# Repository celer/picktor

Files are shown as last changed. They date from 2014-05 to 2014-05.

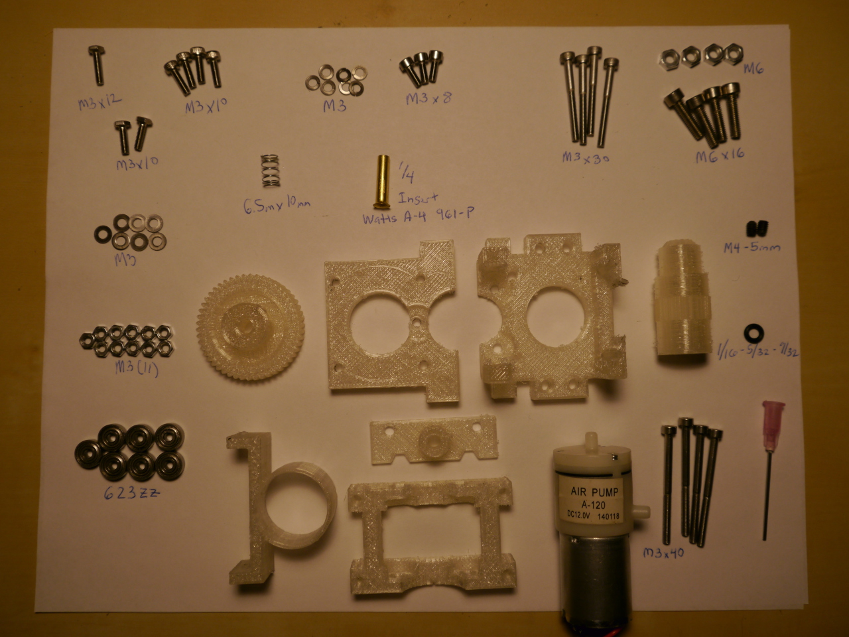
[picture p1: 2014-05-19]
images/parts.jpg

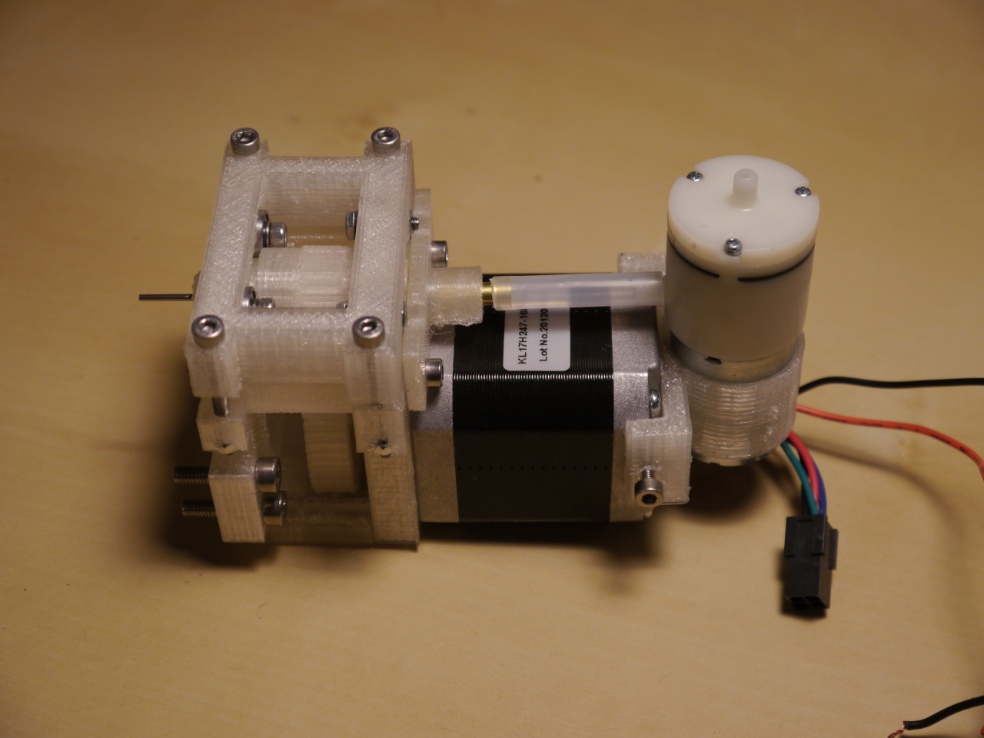
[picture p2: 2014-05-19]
images/left_side.jpg

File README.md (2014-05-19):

Introduction
============

Picktor is a 3D printable pick and place head for surface mount electronics components. 

It mounts on a 3D printer and uses a needle and vacuum pump to pick up small components and place them on a circuit board. 

To keep things simple the included software assumes you've taped/attached one or more circuit boards and bits of 
component tape to your print bed, and then told the software where your circuit boards and component tapes are. 

You can see it work here:

Video of it working (http://www.youtube.com/watch?v=OV2Zr3X-EQc)

*While I've tested this and it seems to work for me consider it a proof of concept, it may not work for you, it may break your printer, it may ruin your circuit boards...*

Modifying the 3D model
======================

Modify the model/picktor.scad, and run Make

Building the Picktor PNP Head
=============================

Here is what you'll need

![Parts] (https://raw.githubusercontent.com/celer/picktor/master/images/parts.jpg)

  * A 3D printer
  * All the parts in the model directory printed out
  * 4x M3 x 40MM Cap screws [1]
  * 7x 623ZZ Bearings [2]
  * 11x M3 nuts [3]
  * 7x M3 flat washers [3]
  * 7x M3 lock washers [3]
  * 3x M3 x 10MM hex head screws [3]
  * 4x M3 x 10MM cap head screws [1]
  * 3x M3 x 8MM cap screws [1]
  * 4x M3 x 30MM cap screws [1]
  * 2x M4 x 5MM set screws 
  * 1x 1/16 x 5/32 x 9/32 o-ring [4]
  * 6.5mm x 10mm spring [5]
  * 1/4 Brass insert from the Watts A-4 961 P plumbing kit [6]
  * 12v Vacuum Pump [7]
  * 18guage dispensing needle 
  * 1/4 ID nylon hose 
  * white lithium grease

### Where to get stuff

  - [1] http://www.ebay.com/itm/M3-0-50-X-6MM-THRU-30MM-STAINLESS-STEEL-METRIC-SOCKET-HEAD-C-S-ASSORTMENT-/291147199149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
  - [2] http://www.amazon.com/Bearing-Shielded-Miniature-Bearings-VXB/dp/B002BBF3JO/ref=sr\_1\_1?ie=UTF8&qid=1400472770&sr=8-1&keywords=623zz
  - [3] http://www.ebay.com/itm/M3-0-50-X-6MM-THRU-20MM-STAINLESS-STEEL-HEX-HEAD-CAP-SCREW-BOLT-ASSORTMENT-/291140653858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
  - [4] http://www.harborfreight.com/382-piece-o-ring-assortment-67554.html
  - [5] http://www.amazon.com/Tradespro-835798-Spring-Assortment-200-Piece/dp/B003L0LEJM/ref=sr\_1\_1?s=hi&ie=UTF8&qid=1400472954&sr=1-1&keywords=835798
  - [6] http://www.homedepot.com/p/Watts-1-4-in-Brass-Compression-Nut-with-Insert-A-4/100638289
  - [7] http://www.ebay.com/itm/DC12V-DC-micro-vacuum-pump-Pumping-air-pump-30Kpa-Air-sampling-/191113084674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
  - [8] http://www.amazon.com/XCSOURCE%C2%AE-Waterproof-Microscope-Inspection-Borescope/dp/B00JD4Y56Y/ref=sr\_1\_sc\_1?s=industrial&ie=UTF8&qid=1400475218&sr=1-1-spell&keywords=xcsouce+microscope

### Optional Items
 
  * 1 USB camera [8]

(This camera is kind of dissapointing ... see the video quality in the link above)

For mounting to the printer

  * 4x M6x16 cap head screws
  * 4x M6 nuts

Things you might have from your existing printer

  * NEMA 17 stepper motor

### Assembling the top mount

Put an M3 nut in the recessed part of the top mount. In order place a lock washer, 623ZZ bearing 
and flat washer on an M3x10 hex head bolt. Then screw the M3 bolt into the recessed nut. 

### Assemble the stepper gear

Insert the two M4 x 5MM set screws into the stepper gear. You may need an M4 tap to properly thread
the set screws into the gear. 

### Place the top mount on the stepper

Place the top mount on the stepper motor, so that the recessed nut is pressed against the stepper
motor. (It may require some pressure to put the top mount on the stepper motor. 
 
### Place the stepper gear on the stepper motor

Place the stepper gear on the stepper motor shaft, but do not tighten the set screws yet. 

### Assemble the bottom mount

Insert two M3 nuts into the recessed cut outs on the bottom of the mount. Assemble two sets of screws and bearings. 

Place a lock washer, bearing and flat washer on an M3 x 10MM cap screw and screw them into the recessed nuts on the mount.

### Put the top and bottom mount together

Place the bottom mount on the top mount and screw them togther using the 4 M3 X 40MM screws. 

### Assemble the front mount

Place 4 M3 nuts on the recessed cut outs.

Assemble 4 sets of M3 x 10mm bolts (two hex head and two cap screw) with washers and bearings. 

Utilize the 2 hex head bolts on the top part of the front mount (it has a larger diameter circle cut out of it)

Utilize the 2 cap screws on the bottom part of the front mount. 

### Prepare the tool gear

File and sand the surfaces of the tool gear that contact the bearings. 

Insert the 17 gauge need into the center of the tool gear (you may need to drill out the hole
in the tool gear). Using white lithium grease grease the o-ring and press it on top of the 17 gauge
needle. The o-ring must press on the top of the needle opening (the pink part). Apply grease to the
top of the o-ring.

Using a marker, mark the top of the tool gear on one of the lines. 

### Place the tool gear between the front mount and mounts attached to the stepper motor. 

Place the tool gear between the front mount and mounts attached to the stepper motor. 
Adjust the stepper gear so that the teeth on the stepper gear align with the teeth on the tool gear - tighten the set screws. 

Check to make sure that the tool gear spins freely, if not check for clearences against the various bolt heads, uneven surfaces
on the tool gear and lastly that all the bearings spin freely. 

### Attach the front mount to the other mounts

Place the 4 M3 nuts into the recessed cut outs on the front of the bottom mount. 

Using the 4 M3 x 30 MM screws attach the front mount to the bottom mount. 

### Assemble the air house mount

Place the spring on top of the brass insert, and then insert into the printed air hose mount. Attach the air house mount to the top of the top mount using 2 M3x8MM cap head screws. The brass insert
should press against the top of the o-ring in the tool gear. 

### Assemble the pump mount

Thread an M3 X 8mm screw into one of the holes on the side of the air pump mount. 

Insert the vacuum pump into the vacuum pump mount. Place the vacuum pump mount on top of the stepper motor, and cut an appropriate length of 1/4 nylon hose to fit between the pump and
air hose mount. 

Using it
========

 *There is no warranty, use this at your own risk*
 
### Attach the picktor head to your 3D printer

In the model/picktor.scad file there is a function mount\_ordbot which generates the appropriate
mount setup for the ordbot, create a new function which is appropriate for your printer. 

### Wire up the stepper motor to where your extruder was

If you used the same stepper motor which powered your extruder, then simply hook it back up. 

### Attach the vacuum pump to one of the power supplies (I used the power supply which was running the fan for my extruder)

You'll need some way to to turn on and off the vacuum pump. On my printer I'm using the same pins that were used to power
the cooling fan for the extruder. In my case it is PIN 4 and I use the gcode command 'M42 P4 S255' to turn on and off the vacuum pump. 

Both Marlin and Sprinter firmware don't buffer the M42 command, so you will need to modify your firmware to call st\_synchronize(); immediately after
the M42 command is recieved.

In sprinter, this functionality can be enabled by enabling the macro CHAIN\_OF\_COMMAND

https://github.com/kliment/Sprinter/blob/master/Sprinter/Sprinter.pde#L1446

In Marlin you'll need to add the line st\_synchronize()

https://github.com/ErikZalm/Marlin/blob/Marlin_v1/Marlin/Marlin_main.cpp#L1798

It should look like this after your modification:

```c
    case 42: //M42 -Change pin status via gcode
      if (code_seen('S'))
      {
        int pin_status = code_value();
        int pin_number = LED_PIN;

        st_synchronize();

      //...
```

### Level our printer bed so that it just barely touches the placer needle

The included software in /src is designed to utilize a needle which almost touches the print bed. 

### Configure the software

To run the included software you'll need Python 2.7 and to create an appropriate configuration file. 

So the software makes some assumptions, it assumes that you've taped your circuit board(s) to the print bed, along with some 
component tapes. And that you've put some basic reference information in the config.yml.

### Tape the circuit board to your printer bed

Tape one or more circuit boards to your print bed. And in the config.yml specify the location of a single component 
on the board. Once you run the software it will tell you where it expects the second reference to be on your print bed. 

### Tape the component tapes to your printer bed

Tape one or more tapes of componets to your print bed. Specify in the config software where the first component is 
on the print bed. Once you run the software it will tel you where it expects the last component to be on the print bed.

### Print! 

Do a few test runs before you assume all is good!

### Adjust any out of place components

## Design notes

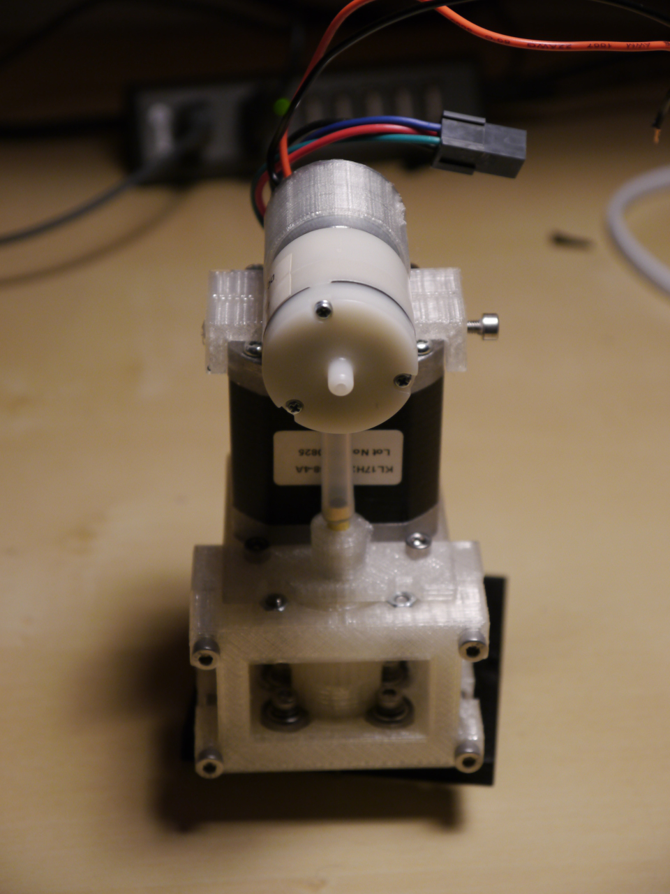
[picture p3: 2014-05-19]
images/front.jpg

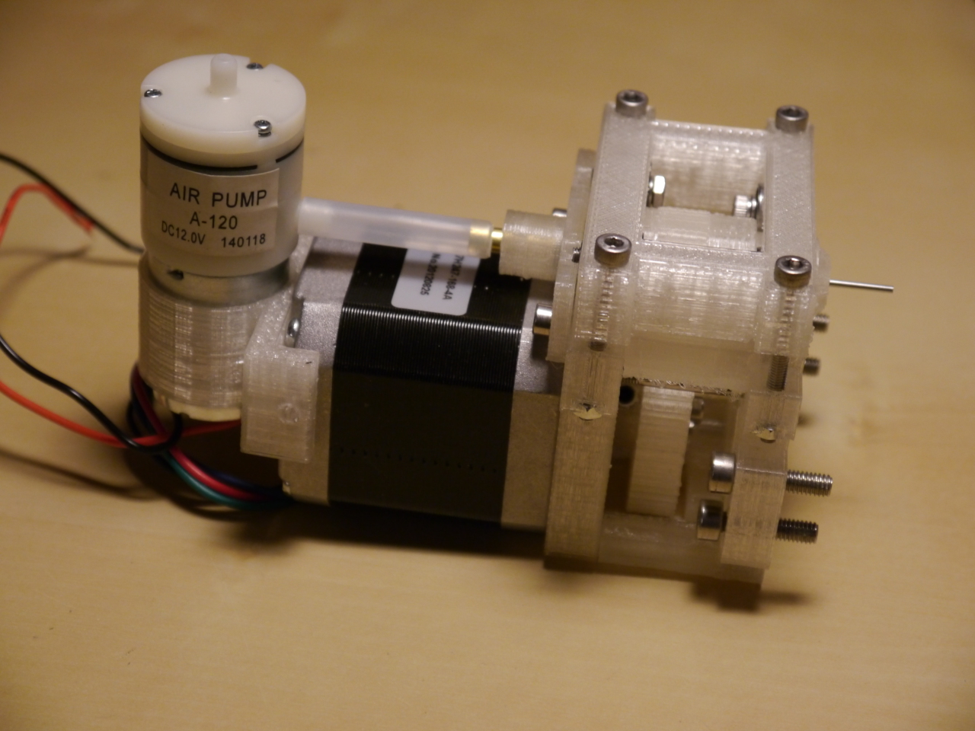
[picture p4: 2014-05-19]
images/right_side.jpg

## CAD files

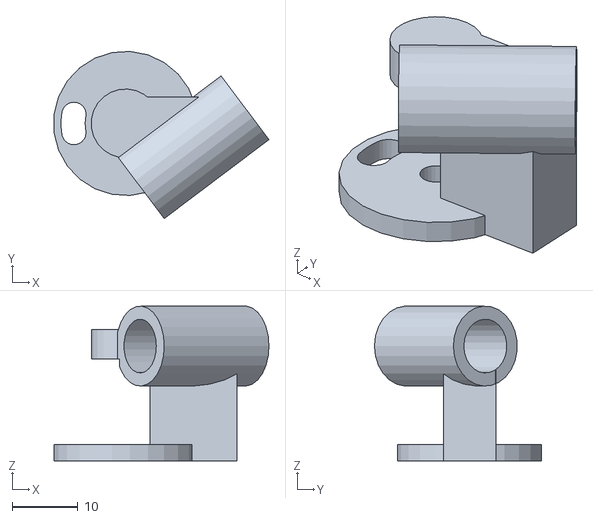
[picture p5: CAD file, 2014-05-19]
model/picktor_camera_mount.stl
32.8 x 25.5 x 23.6

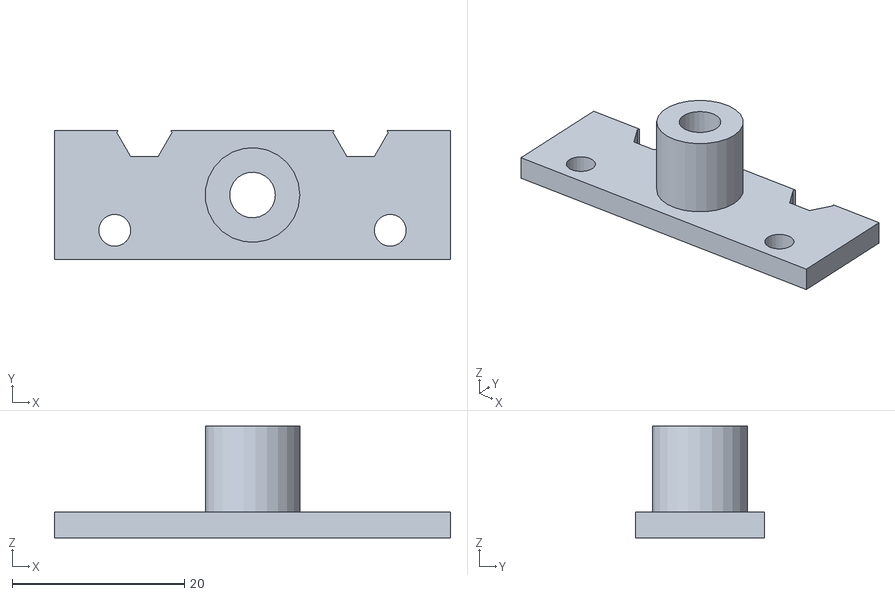
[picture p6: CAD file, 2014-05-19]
model/picktor_air_hose_mount.stl
46.0 x 15.0 x 13.0

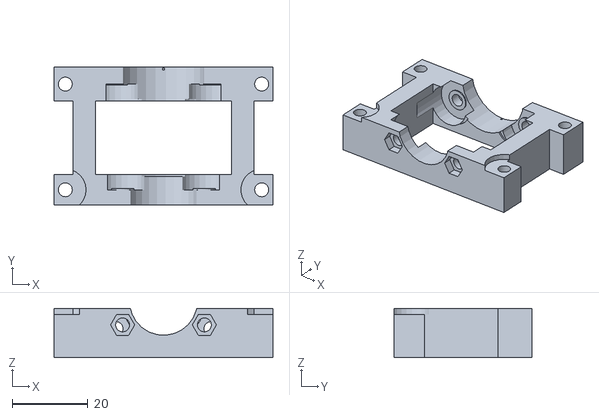
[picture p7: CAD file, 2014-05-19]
model/picktor_mount_front.stl
58.0 x 36.5 x 13.0

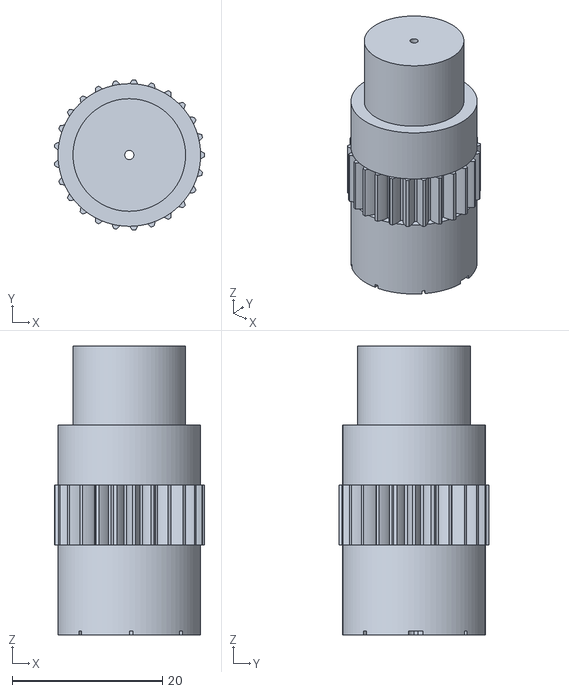
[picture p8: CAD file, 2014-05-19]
model/picktor_tool_gear.stl
20.0 x 20.0 x 38.5

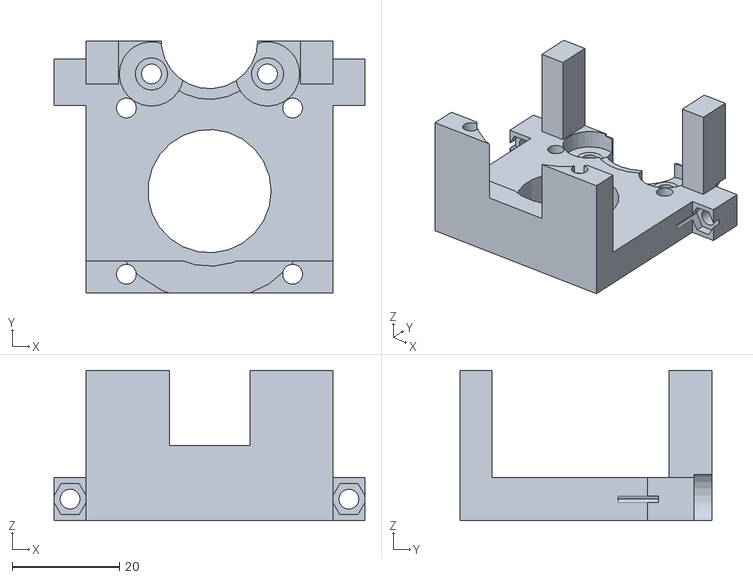
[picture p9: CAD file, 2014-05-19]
model/picktor_mount_bottom.stl
58.0 x 47.0 x 28.0

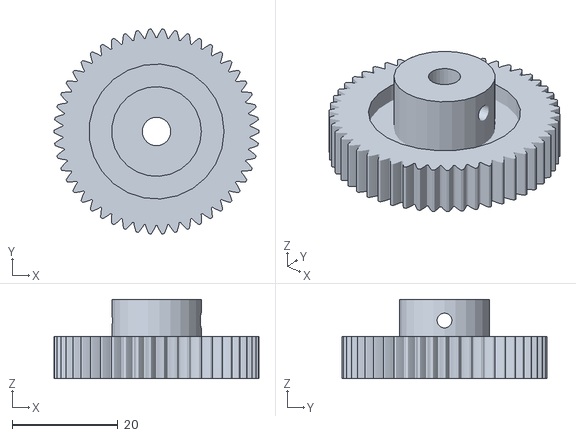
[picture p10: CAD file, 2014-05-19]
model/picktor_stepper_gear.stl
38.8 x 38.8 x 15.0

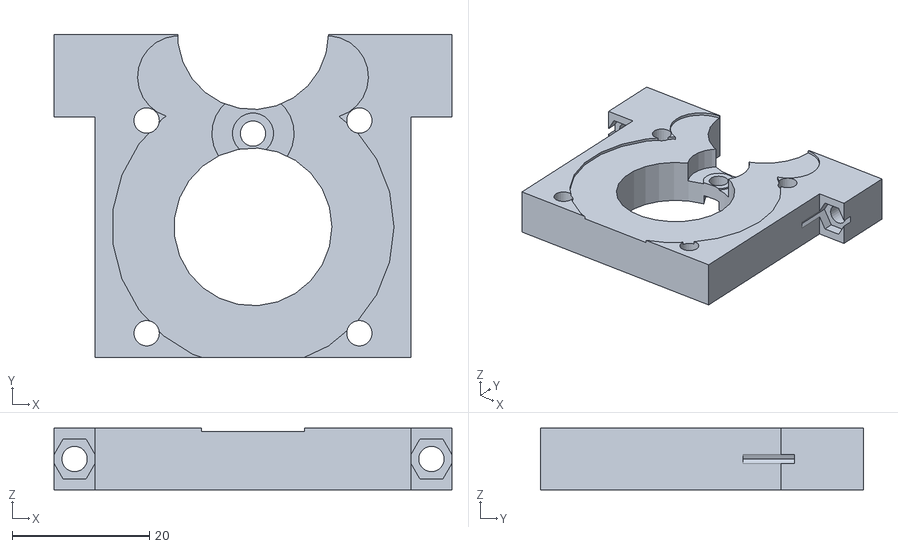
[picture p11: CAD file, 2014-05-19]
model/picktor_mount_top.stl
58.0 x 47.0 x 9.00

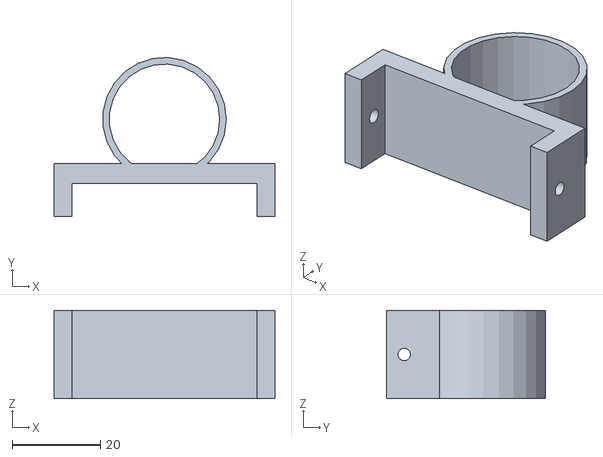
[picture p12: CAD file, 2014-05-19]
model/picktor_pump_mount.stl
50.0 x 36.0 x 20.0

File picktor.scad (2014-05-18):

//If these don't load for you, make sure you have the latest version of openscad
include <MCAD/involute_gears.scad>;
include <MCAD/stepper.scad>;
include <MCAD/nuts_and_bolts.scad>;

//Set the fineness
$fn=25;


//How far the tool gear is from the stepper gear
gear_offset=28.1;
//Top and bottom tool gear diameters
tool_top_gear_diameter=19;
tool_bottom_gear_diameter=15;


needle_diameter=1.23;


//Setup for M3 hardware
screw_size=3;
screw_hole=3.7;
screw_hole_threaded=2.8;
screw_cap=6.5;
screw_cap_height=4;

module bearing_cutout(){
	difference(){
		cylinder(r=12/2,h=4,center=true);
		translate([0,0,-4/2]) cylinder(r=6/2,h=0.6,center=true);
		translate([0,0,4/2]) cylinder(r=6/2,h=0.6,center=true);
	}
}

module bearing_screw_cutout(screw_length=15,nut_hole_depth=0){
	translate([0,0,-2]){
		translate([0,0,3.5]) cylinder(r=screw_cap/2,h=screw_cap_height);
		translate([0,0,-screw_length+4]) cylinder(r=screw_hole/2,h=screw_length);
		for(i=[0:1:nut_hole_depth]){
			rotate([0,0,30]) translate([0,0,-screw_length+4-i]) nutHole(screw_size);
		}
	}
}

module brass_stub(){
	cylinder(r=(4.4+0.90)/2,h=18.7);
	translate([0,0,18.7-6]) cylinder(r=7/2,h=6);
}

module picker_needle(n=needle_diameter){
  translate([0,0,0]) cylinder(r=7.8/2,h=2.5);
  translate([0,0,2.5]) cylinder(r1=6.8/2,r2=6.5/2,h=17);
  cylinder(r=n/2,h=50.50);
}

module tool_gear(n=needle_diameter){
	difference(){
		union(){
			gear(circular_pitch=135,number_of_teeth=25,hub_thickness=0,bore_diameter=5.40,rim_thicknes=15);
			translate([0,0,14]) cylinder(r=tool_bottom_gear_diameter/2,h=25,center=true,$fn=80);
			translate([0,0,-6]) cylinder(r=tool_top_gear_diameter/2,h=12,center=true,$fn=80);
			translate([0,0,12]) cylinder(r=tool_top_gear_diameter/2,h=8,center=true,$fn=80);
			//So I wanted some way for the tool gear to turn a part dispensor ... 
			//translate([0,0,26]) scale(0.20) bevel_gear(pressure_angle=40,cone_distance=50);
		}

		rotate([0,0,0]) translate([9.25,0.25,-12]) cylinder(r=2/2,h=0.5);

		for(a=[0:360/4:360]){
			rotate([0,0,a]) translate([6,0,-12]) cube([5,0.5,0.5]);
		}
		for(a=[0:360/4:360]){
			rotate([0,0,a+45]) translate([8,0,-12]) cube([5,0.5,0.5]);
		}

		translate([0,0,-12]) picker_needle(n);
		
	}
	
}

module tool_gear_cutout(){
	translate([0,0,8]) cylinder(r=tool_bottom_gear_diameter/2+1.5,h=40,center=true);
	translate([0,0,-2.5]) cylinder(r=tool_top_gear_diameter/2+1.5,h=20,center=true);
    translate([0,0,7.5]) cylinder(r=tool_top_gear_diameter/2+1.5,h=18,center=true);
}

module stepper_gear_cutout(){
	translate([0,0,-4]) cylinder(r=41.1/2,h=14);
	translate([0,0,0]) cylinder(r=28/2,h=16);
}


module stepper_gear(){
	difference(){
		gear(circular_pitch=135,number_of_teeth=50,hub_thickness=15,bore_diameter=5.40,hub_diameter=17);
		translate([0,0,11]) rotate([0,90,0]) cylinder(r=screw_hole_threaded/2,h=20,center=true);
	}
}

module tri_rotate(distance,offset=30){
	for(a=[0:360/3:360]){
		rotate([0,0,offset+a]) translate([distance,0,0]) children();
	}	
}

module stri_rotate(distance,offset=30){
	
	rotate([0,0,offset+120]) translate([distance,0,0]) children();
	rotate([0,0,offset+240]) translate([distance,0,0]) children();

	rotate([0,0,offset+60]) translate([distance,0,0]) children();
	rotate([0,0,offset-60]) translate([distance,0,0]) children();

}

module quad_rotate(distance,offset=30){
	for(a=[0:360/4:360]){
		rotate([0,0,offset+a]) translate([distance,0,0]) children();
	}	
}

module bearing_set(){
	tri_rotate((tool_top_gear_diameter+10)/2){
		bearing_cutout();
	}
}

module stepper_screw_holes(){
	for(x=[-15.5,15.5]){
		for(y=[-15.5,15.5]){
			translate([x,y,0]) children();
		}
	}
}


mount_height=36;
bearing_tightness=0.40;


module camera_mount(){
	camera_d=8.2;
	camera_angle=-53;
	difference(){
		union(){
		translate([15,0,0]) rotate([0,camera_angle,0]){
			 translate([0,0,6]) union(){
				cylinder(r=(camera_d+4)/2,h=20,center=true);
				
			 }	
			 //line pointing at where the camera would aim	
			 //cylinder(r=1/2,h=110,center=true);
		}
		translate([5+2,7.5,0]) cube([20,20,8],center=true);
		rotate([90,0,0]) difference(){
			cylinder(r=10.5/2,h=5,center=true);
			cylinder(r=screw_hole/2,h=5,center=true);

			
		}


		difference(){
		translate([0,13+3.25,0]) rotate([90,0,0]) difference(){
			union(){
				cylinder(r=22/2,h=2.5,center=true);
			}
			
		}
		for(a=[-10:1:10]){
			rotate([0,a,0]){
				translate([-8,0,0]) rotate([90,0,0]){
					cylinder(r=screw_hole/2,h=100,center=true);
				}
			}
		}
	
		}
	}
	
		translate([0,13+3.25,0]) rotate([90,0,0])  cylinder(r=screw_hole/2,h=25,center=true);	
		translate([0,15,0]) rotate([90,0,0]) cylinder(r=11/2,h=13);
		translate([15,0,0]) rotate([0,camera_angle,0]){
			translate([0,0,6]) cylinder(r=camera_d/2,h=25,center=true);
		}
	}
}


module mount_cutout(){
	
	translate([0,gear_offset+10,-mount_height/2+6]) cube([0.5,tool_bottom_gear_diameter/2+1,0.5],center=true);


	for(y=[-26,26]){
		translate([y,50,20]) rotate([90,0,0]) cylinder(r=screw_hole/2,h=40);
		translate([y,47,20]) rotate([90,0,0]) cylinder(r=screw_cap/2,h=screw_cap_height);

		translate([y,50,12-20]) rotate([90,0,0]) cylinder(r=screw_hole/2,h=40);
		translate([y,47,12-20]) rotate([90,0,0]) cylinder(r=screw_cap/2,h=screw_cap_height);

		//cutout for the camera hinge
		translate([y,gear_offset,20]) rotate([90,0,0]) cylinder(r=11/2,h=7,center=true);

		translate([y-8,gear_offset+12,20]) rotate([90,0,0]) cylinder(r=screw_hole_threaded/2,h=15,center=true);

		for(i=[0:1:5]){
			translate([y,18-i,20]) rotate([90,0,0]) scale(1.05) nutHole(screw_size);
			translate([y,18-i,12-20]) rotate([90,0,0]) scale(1.05) nutHole(screw_size);
		}
	}


	for(x=[-16,16]) {
		translate([x,24,-13]) cylinder(r=screw_hole_threaded/2,h=10,center=true);
		translate([x,24,-17.5]) cylinder(r=screw_hole/2,h=10,center=true);
	}

	translate([0,gear_offset,-mount_height+6]) brass_stub();

	translate([0,0,6]){
		cylinder(r=23/2,h=mount_height+5,center=true);
		stepper_screw_holes(){
			cylinder(r=screw_hole/2,h=mount_height+5,center=true);
			translate([0,0,mount_height/2-1.5]) cylinder(r=screw_cap/2,h=screw_cap_height,center=true);
		}
		
	}
	translate([0,gear_offset,0]){
		stri_rotate((tool_bottom_gear_diameter+10)/2,90){
			translate([0,0,18]){
				 bearing_cutout();
				 translate([0,0,-22]) cylinder(r=12/2,h=23);
				 mirror([0,0,1]) bearing_screw_cutout(8,1);
			}
		}
		tri_rotate((tool_top_gear_diameter+10)/2,30){
			translate([0,0,-6]){
				bearing_cutout();
				cylinder(r=12/2,h=10);
				bearing_screw_cutout(9,3);
			}
		}
	}
	stepper_gear_cutout();
	translate([0,gear_offset,0]) tool_gear_cutout();
}

module mount_shape(){
	
	translate([0,14,20]) cube([46,66,8],center=true);
	translate([-19,43,10]) cube([8,8,mount_height-8],center=true);
	translate([19,43,10]) cube([8,8,mount_height-8],center=true);

	for(i=[-21,21]){
		translate([i,35,10]) cube([4,9,mount_height-8],center=true);
	}
	
	for(i=[-20,20]){
		translate([i,22,10]) cube([6,12,mount_height-8],center=true);
	}
	translate([0,-16,10]) cube([46,6,mount_height-8],center=true);
}


module mount(){
	difference(){
		mount_shape();
		translate([0,gear_offset+1,0]) cube([50,3,50],center=true);
    		mount_cutout();
	}
}

module mount_top(){
	difference(){
		union(){
			translate([0,4.5,-8]) cube([46,47,9],center=true);
			translate([0,22,-8]) cube([58,12,9],center=true);
		}
		mount_cutout();
	}
}

module mount_bottom(){
	difference(){
		union(){
			translate([0,4.5,20]) cube([46,47,8],center=true);
			translate([0,22,20]) cube([58,12,8],center=true);
	
			for(i=[-20,20]){
				translate([i,24,10]) cube([6,8,mount_height-8],center=true);
			}
			
			translate([0,-16,10]) cube([46,6,mount_height-8],center=true);
		}
		mount_cutout();
	}
}

module mount_ordbot(){
	
	xdiff = 84.972-35.028;
	ydiff = 10;
	difference(){
		union(){
			translate([0,0,20]) cube([xdiff+10,ydiff+10,8],center=true);
			mount_bottom();
		}
		mount_cutout();
		for(x=[-xdiff/2,xdiff/2]){
			for(y=[-ydiff/2,ydiff/2]){
				translate([x,y,22.5]) cylinder(r=4.2/2,h=25,center=true);
			}
		}	
	}
}



module air_hose_mount(){
	difference(){
		union(){
			translate([0,gear_offset,-14]) cube([46,15,3],center=true);
			translate([0,gear_offset,-18]) cylinder(r=11/2,h=15,center=true);
		}
		mount_cutout();
	}
}

module mount_front(){
	difference(){
		union(){
			//translate([-19,43,10]) cube([8,8,mount_height-8],center=true);
			//translate([19,43,10]) cube([8,8,mount_height-8],center=true);

			
			translate([0,36.5,20]) cube([58,13,8],center=true);
			translate([0,36.5,-8]) cube([58,13,9],center=true);
	
			for(i=[-21,21]){
				translate([i,36.5,10]) cube([6,13,mount_height-8],center=true);
			}
		}
		mount_cutout();
	}
}
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

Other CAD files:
model/picktor.scad

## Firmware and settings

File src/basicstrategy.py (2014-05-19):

from strategy import Strategy
from board import Board
from part import PartPlacement
from board import BoardLocation
from placer import Placer
from part import TapeTemplate
from pprint import pprint 
from picker import Picker
from part import Tape
from job import Job
from job import JobStep

class BasicStrategy(Strategy):
  def __init__(self,config):
    Strategy.__init__(self,config)
    self.placer = Placer(config)
    self.picker = Picker(config)

  def pickAndPlace(self,jobName,stepName,stream):
    boards={}
    jobs={}
    tapes={}
    tapeTemplates={}

    if self.config['boards']:
      for board in self.config['boards']:
        newBoard = Board(self.config)
        if 'name' in board:
          newBoard.setName(board['name'])

        if 'placements' in board:
          newBoard.setPlacements(PartPlacement.readFile(board['placements']))
        else:
          print "No placement specified for board:",board['name']

        if 'height' in board:
          newBoard.height=board['height']; 
        
        boards[newBoard.name]=newBoard
    

      # Load up the tape templates
      for tapeTemplate in self.config['tapeTemplates']:
        template = TapeTemplate()
        
        if 'name' in tapeTemplate:
          template.name = tapeTemplate['name']
        else:
          raise Exception("Missing tape template name")
        
        
        for name in tapeTemplate:
          if hasattr(template,name):
            setattr(template,name,tapeTemplate[name])
      
        tapeTemplates[template.name]=template;

      # FIXME Should validate the tapetemplate here 
        
  
      for tape in self.config['tapes']:
        if not 'name' in tape:
          raise Exception("No name specified for tape")
        if not 'template' in tape:
          raise Exception("No template specified for tape")
        if not tape['template'] in tapeTemplates:
          raise Exception("Invalid tape template specified:",tape['template'])
       
        partTape = Tape()

        for name in tape:
          if hasattr(partTape,name):
            setattr(partTape,name,tape[name])

        partTape.tapeTemplate=tapeTemplates[tape['template']]

        tapes[partTape.name]=partTape


      for job in self.config['jobs']:
        j = Job()

        for name in job:
          if hasattr(j,name) and name!="steps" and name!="boards":
            setattr(j,name,job[name])

        for board in job['boards']:
          if not 'name' in board:
            raise Exception("Invalid board specified")
          if not board['name'] in boards:
            raise Exception("Invalid board name:"+board['name'])
          j.addBoard(boards[board['name']], board['reference'],board['x'],board['y'], board['second_reference'])
          
        for step in job['steps']:
          js = JobStep()
        
          for name in step:
            if hasattr(js,name):
              setattr(js,name,step[name])
          j.steps.append(js)

      jobs[j.name]=j

      ##################################

      #1 Get the current job and step

      if not jobName in jobs:
        raise Exception("Invalid job name:"+jobName)
      
      currentJob = jobs[jobName]    

      currentStep = next((step for step in currentJob.steps if step.name == stepName), None)

      #2 Setup the placer with the boards
 
      stream.write("G28\n")
      stream.write("M302\n")
      stream.write("M92 E400\n")
 
      for board in currentJob.boards:
        self.placer.addBoard(board)

      self.placer.organizeBoards(stream)

      #3 Setup the picker with the tapes

      for tape in currentStep.tapes:
        self.picker.addTape(tapes[tape])

      self.picker.organizeTapes(stream)

      self.picker.generatePlacements(self.placer.boards)

      while True:
        pn = self.picker.pickPart(stream);
        if None==pn:
          break
        self.placer.placePart(pn.board,pn.placement,pn.tape,stream);

      

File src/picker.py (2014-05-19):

class PickerPlacement:
  def __init__(self,tape,board,placement):
    self.tape=tape
    self.board=board
    self.placement=placement

class Picker:
  def __init__(self,config):
    self.config=config
    self.tapeTemplates={}
    self.tapes=[];

  def addTape(self,tape):
    self.tapes.append(tape)

  def organizeTapes(self,stream):
    for tape in self.tapes:
      stream.write("\n;Please make sure the tape "+tape.name+":")
      stream.write("\n;\tHas the first item at "+str(tape.origin_x)+","+str(tape.origin_y))
      stream.write("\n;\tAnd has the last item at "+str(tape.origin_x+tape.numberOfParts*tape.tapeTemplate.partDistance)+","+str(tape.origin_y)+"\n")
 
  def generatePlacements(self,boards):
    self.placements=[]

    for tape in self.tapes:
      partsUsed=0
      for board in boards:
        for placement in board.board.placements:
          if  tape.value == placement.value and placement.package == tape.tapeTemplate.package:
            # This needs to do this for as many parts as the tape has on it ... 
            partsUsed+=1
            if(partsUsed > tape.numberOfParts):
              break
            self.placements.append(PickerPlacement(tape, board, placement))
     
  def pickPart(self,stream):
    if(len(self.placements)>0):
      part = self.placements.pop(0)

      # advance tape
      # take part 
      self.pickUpPart(part.tape,stream)

      return part
    else:
      return None

  def advanceTape(self,tape,stream):
    "this would advance the picker or tape"
    tape.currentPart=tape.currentPart+1      

  def pickUpPart(self,tape,stream):
    "pick up the part"
    # Move to where we thing the part is
    stream.write("\n; Pick up the part from "+tape.name+"\n");
    stream.write("G1 E0\n")
    stream.write("G1 X"+str(tape.origin_x+tape.currentPart*tape.tapeTemplate.partDistance)+" Y"+str(tape.origin_y)+" Z20 F3000\n")
    # Visit the parts surface
    stream.write("G1 X"+str(tape.origin_x+tape.currentPart*tape.tapeTemplate.partDistance)+" Y"+str(tape.origin_y)+" Z"+str(tape.tapeTemplate.partHeight)+" F200\n")
    # Turn on the vacuum
    stream.write("M42 P4 S255\n");
    # Dwell
    stream.write("G4 P400\n");
    # Left the part upwards
    stream.write("G1 X"+str(tape.origin_x+tape.currentPart*tape.tapeTemplate.partDistance)+" Y"+str(tape.origin_y)+" Z20 F1000\n")
    
    self.advanceTape(tape,stream)

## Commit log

2014-05-19 Updated based on first test with the printer
2014-05-19 Updated to included generated versions of the models
    [picktor.scad, picktor_air_hose_mount.stl, picktor_camera_mount.stl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]
